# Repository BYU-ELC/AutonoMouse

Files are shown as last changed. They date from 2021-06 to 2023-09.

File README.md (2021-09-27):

# AutonoMouse

## Introduction
Lightweight and low cost autonomous robotics platform for students to gain skills and have fun!

There are two version to this project. 

V1's objective is to build a small autonomous car using Arduino Nano as a controller. The car drives forward until sensing an object. When it senses an object it pivots to both sides to find both distances to the nearest object. It then chooses to travel the distance that is greater. 

V2's objective is to build a similiar autonomous car using ESP32 as a controller. However, this version
allow's the user to put the car into remote control mode where the user can control the car via bluetooth
using an Android smartphone. This doesn't work with an IPhone because there are no opensource bluetooth apps 
that in the App Store. 

## V1 Things to Change
More accessibility Linux and Apple users. Document how to download Arduino IDE and how to interfaces with Arduino devices.

## V2 Things to Change
Finish development for V2. Mostly needs work with the servos.

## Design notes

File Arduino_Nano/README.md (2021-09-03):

# Arduino Nano version of the Autonomouse

## PCB
Recommended: Use gerber files in Build_Files->Chassis1.1->Chasiss1.1_2021-09-01.zip. 

## Acrylic Base
Laser cut the acrylic base using Arduino_Nano_chassis.svg in Build_Files folder. 

## Labs
Follow the labs sequentially in Labs folder.

## Code
Code is provided along with most labs. Upload the code to Arduino Nano using a USB A-Mini and the Arduino IDE.

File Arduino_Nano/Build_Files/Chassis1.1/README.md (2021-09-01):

Chassis1.1 is a revision of the previous Chassis1.0.

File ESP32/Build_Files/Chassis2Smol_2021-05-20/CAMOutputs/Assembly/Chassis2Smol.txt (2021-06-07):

Partlist exported from E:/BYU/ECEN_191_Proj/Chassis2Smol.sch at 5/20/2021 1:57 PM

Qty Value             Device               Package             Parts       Description                                                                                                     POPULARITY PROD_ID    VALUE
1                     CONN_02              1X02                9V_BATT     Multi connection point. Often used as Generic Header-pin footprint for 0.1 inch spaced/style header connections                            
1                     CONN_04PTH           1X04                HC-SR04     Multi connection point. Often used as Generic Header-pin footprint for 0.1 inch spaced/style header connections            CONN-09696      
2                     PINHD-1X19           1X19                JP1, JP2    PIN HEADER                                                                                                      1                          
1   0.1uF             0.1UF-KIT-EZ-50V-20% CAP-PTH-SMALL-KIT   C2          0.1µF ceramic capacitors                                                                                                   CAP-08370  0.1uF
1   0.33uF            0.1UF-KIT-EZ-50V-20% CAP-PTH-SMALL-KIT   C1          0.1µF ceramic capacitors                                                                                                   CAP-08370  0.1uF
1   FRAME-BADGE       FRAME-BADGE          DUMMY               U$1                                                                                                                                                    
1   LM7805            LM7805               TO220H              U2                                                                                                                                                     
2   SERVO             SERVO                1X03                LEFT, RIGHT Servo Motor                                                                                                                                
1   SHOP_ESP_SMOLSMOL SHOP_ESP_SMOLSMOL    ESP32-WROOM-32_SMOL U$2                                                                                                                                                    
1   TL36PO            TL36PO               TL3XPO              S1          TINY SWITCH ON - ON                                                                                             2

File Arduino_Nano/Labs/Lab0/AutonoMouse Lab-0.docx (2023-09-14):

# Introduction

## Summary:

This course is intended for beginning ECEN students taking ECEN 191 at BYU. We assume that students taking this course have a high school level education and are not required to know anything about electrical engineering or hobby engineering. If you are a beginner this is the course for you!

## Learning Outcomes:

The final product from this course is a simple autonomous car named the AutonoMouse. Students will learn the following skills while developing their car:

- Learn what Arduino is
- Learn how to solder pins onto a PCB
- Learn how to code an Arduino Nano
- Learn how to prototype with breadboards
- Learn how LEDs work
- Learn about servos and pulse width modulation signals
- Learn about voltage regulators
- Learn how to spin a servo
- Learn how to use a sensor
- Learn about the HC-SR04
- Learn about PCBs
- System integration
- Troubleshooting

## Materials You Need to Buy:

The following materials you will need to buy yourself:

Arduino Nano
Part | Quantity | Unit Price | Subtotal | Notes
1 inch diameter bottle cap | 2 | | $0.00 | Buy your own, Gatorade bottles work best
Zip ties | 3 | $0.03 | $0.09
Arduino Nano | 1 | $4.00 | $4.00
Switch-SPDT-BB | 1 | $0.06 | $0.06
Voltage Regulator (Q-7805c) | 1 | $1.65 | $1.65
0.1 μF Ceramic Capacitors | 1 | $0.06 | $0.06
0.33 μF Ceramic Capacitor | 1 | $0.06 | $0.06
330 Ohm Resistor | 1 | $0.04 | $0.04
9V Battery | 1 | $1.25 | $1.25
Battery Cap | 1 | $0.44 | $0.44
1x3 Male header | 2 | $0.06 | $0.12
1x4 Female header | 1 | $0.08 | $0.08
2x15 Female header | 2 | $0.30 | $0.60 | You will need to purchase 2 10x1 and 2 5x1 female header pins.
Continuous Servo | 2 | $1.80 | $3.60
PCB | 1 | $1.20 | $1.20 | 3 in^2 @ $0.40 per in^2
Ultra-sonic sensor | 1 | $2.20 | $2.20 | Sensor-Ultrasonic used for angry engineers
LED Colored | 1 | $0.05 | $0.05
CABLE-USB A-Mini | 1 | $0.99 | $0.99
Acrylic | 1 | $1.62 | $1.62 | $0.08 per in^2
Laser Time Acrylic | 2 | $0.06 | $0.12
| | Total | $18.23

Buy these from the ELC (CB 416.) This is a requirement for part of this lab. (This table is just an estimate for these parts, pricing may have changed.) Also, take the time to get acquainted with the ELC. It is a valuable resource on campus.

## Project Requests:

Students can request PCBs, Laser Cuts, and 3D prints from the shop staff. There are two of these for this lab: the PCB and acrylic base. The PCB will be milled and acrylic base laser cut by the shop.

### PCB:

We have a number of these PCB’s already fabricated and should be picked up and paid for with the rest of the autonomouse kit.

First, search the GitHub repository in your web browser (https://github.com/BYU-ELC/AutonoMouse). Then navigate to Arduino_Nano->Build_Files->Chassis1.1 and download the zip file, Chasiss1.1_2021-09-27.zip.

Next, search the ELC project request application (https://byu-elc.mendixcloud.com/p/home) and click the button “PCB Mill Request”. Follow the instructions to fill out the form with your information. You will upload the zip file you just downloaded. The area of the PCB is 3in sq. Things to watch out for: select PCB prototyping for “Requested Service”; single-sided for “Single or Double Sided”; BYU ID # (not netID) for Student ID; and Class for “Purpose”. Click submit.

Once PCB is finished the ELC will let you know when to pick it up.

### Acrylic Base:

We have a number of these Acrylic base’s already fabricated and should be picked up and paid for with the rest of the autonomouse kit.

The acrylic base project request process is similar to the PCB.

First, search the GitHub repository in your web browser (https://github.com/BYU-ELC/AutonoMouse). Then navigate to Arduino_Nano->Build_Files and download Arduino_Nano_chassis.svg. This file will allow the shop to laser cut your car’s base.

Next, search the ELC project request application (https://byu-elc.mendixcloud.com/p/home) and click the button “Laser Cut Request”. Follow the instructions to fill out the form with your information. I would like to use acrylic supplied by the shop. Use any available acrylic on hand (unless you would like to provide or choose your own) for “Material”; 1/8th inch for “Thickness”; BYU ID #, (not netID), for Student ID; Class for “Purpose”; and 4.5-inch x 4.5 inch for “Major Dimension for scaling”. Do not forget to upload the .svg you previously downloaded. Click submit.

After your base is finished the ELC will let you know to pick it up.

## Other:

- 2 x 1-inch diameter bottle caps for wheels (Gatorade or milk bottle caps work nicely for this)
- Computer (this is for programing; a laptop works best because you can bring it into the lab, but a desktop at home would also work)

## Tools Required:

You will need access to the following tools. These can be found in student workshops in the ELC CB41, or you may buy your own as part of your personal electronic kit.

- Breadboard
- Jumper Wires
- Hot glue gun + hot glue
- Soldering station

## How to Access Code for the Labs:

In this course you are not required to know how to code; however, you will still need to know how to download and use Arduino IDE to upload code to your Arduino Nano. Each time the labs ask you to download and upload code go to https://github.com/BYU-ELC/AutonoMouse. This is a GitHub repository that stores all the files for this course. If you’re familiar with GitHub you can git clone the repository. If you’re not familiar then navigate to Arduino_Nano/Labs/(lab# that you’re on). The code file is a .ino file. Copy and paste the code into Arduino IDE and you’ll be good.

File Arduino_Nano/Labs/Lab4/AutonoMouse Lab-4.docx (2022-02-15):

# Lab 4-Sensors

## Learning Outcomes:

- Learn how to work a sensor
- Learn about the ultrasonic sensor

## Background:

Electrical engineers use all kinds of sensors for a variety of applications. It could be a LIDAR module on a self-driving car or a thermocouple in an indoor air conditioning system. Regardless, the purpose of sensors are to record some measurement from the outside world, and turn it into an electrical signal which is then analyzed by a device. Different Types of Sensors and their Uses (i.e. Electrical Sensors) (https://www.thomasnet.com/articles/instruments-controls/sensors/)

Sensors first use an electro-mechanical device to measure something in the real world. The sensor then converts the real-world measurement into a digital or analog signal. A digital signal is composed of bits. Each bit is either a low voltage (0) or high voltage (1). This is what computational devices like your computer use. In contrast, an analog signal can exist within a range of voltages, not just high or low. Regardless of the output type, the sensor communicates the data to a controller from processing. After processing, the controller can then act on the world.

With the advent of the internet of things (Internet of things (https://en.wikipedia.org/wiki/Internet_of_things)), sensors are more important than ever. It’s crucial to understand how they work, and how to use them effectively. When using a sensor that you’re unfamiliar with, it is useful to refer to its datasheet—you can find all sorts of useful information there. For our AutonoMouse we will be using HC-SR04 which is an ultrasonic sensor. Read more about it here: How HC-SR04 Ultrasonic Sensor Works & How to Interface It With Arduino (https://lastminuteengineers.com/arduino-sr04-ultrasonic-sensor-tutorial/)

The project objectives for today’s lab are to:

1) Correctly set up the HC-SR04 ultrasonic sensor

2) Read the data using Arduino’s serial monitor.

### Part 1 Ultrasonic Sensor Circuit:

Build the following circuit.

1. Put Arduino Nano into the center of the breadboard
2. Put wires connect the following pins (Arduino Nano on left, HC-SR04 on right)
  a. 5-volt pin (5V) and VCC
  b. Pin 6 (D6) and TRIG
  c. Pin 7 (D7) and ECHO
  d. Ground pin (GND) and GND

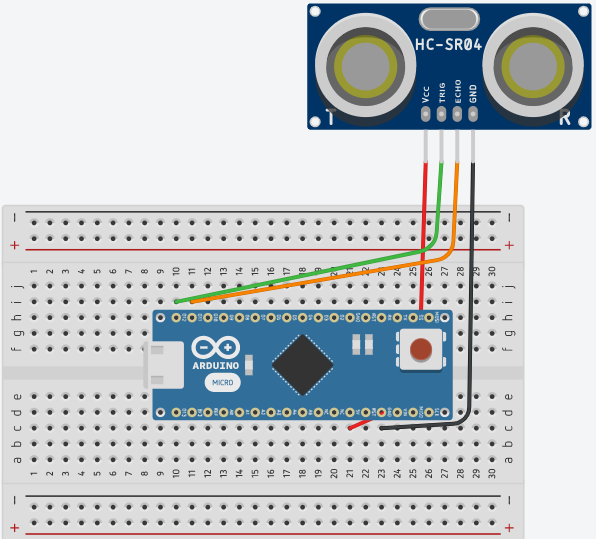
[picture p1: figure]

Ultrasonic Sensor Circuit from Tinkercad

### Part 2 Reading via Serial Monitor:

Copy and upload the code provided with this lab on GitHub to the Arduino. Once the code is successfully uploaded, open a serial monitor through Arduino IDE by clicking the serial monitor button in the top right corner. You should see another window open that provides data from the ultrasonic sensor. Make sure that the baud rate is set to 9600 or else you will see nothing in the serial monitor. The baud rate is the rate information is based through. Try moving the sensor around and get a feel for its range and accuracy. Make sure it works correctly or else your car will not be able to stop in the next lab.

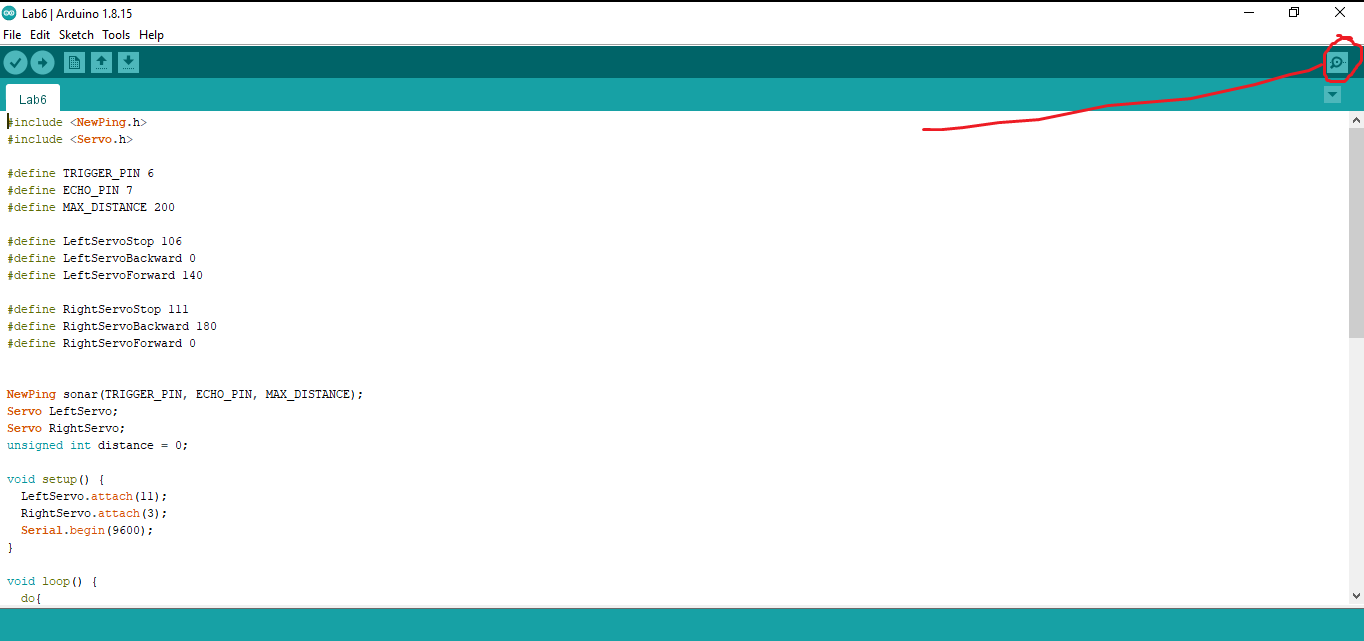
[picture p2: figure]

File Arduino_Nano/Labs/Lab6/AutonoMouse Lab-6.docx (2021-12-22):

# Lab 6-Integration

## Learning Outcomes:

- System integration
- Troubleshooting

## Background:

Up to this point we’ve only tested individual systems of the AutonoMouse (i.e. servos, ultrasonic range finder, PCB). Today we’ll be integrating these subsystems into a whole. This process is called system integration. Integration can sometimes be frustrating because you might not know what system or component is not working. The best thing to do is be patient and logically troubleshoot one thing at a time until you can determine the thing that is not working.

### Part 1 Build:

The first thing we’ll do is attach all our components to our acrylic base mechanically. Then we’ll start connecting the electronics.

1. Use a Phillips screwdriver to poke a hole through the center of your wheels
2. Use hot glue to glue your wheels to your servo mounts
3. Add the screw provided with your servos for extra support
4. Put a dot of hot glue around the circumference of your wheels about every 1cm (this helps the wheel maintain traction
5. Hot glue and zip tie your servos to the two wings of your board
6. Zip tie your battery to the end of the board. Make sure that you insert the zip in the correct manner to create a caster. (From the bottom, insert it through the hole closest to the edge) Check that it’s inserted correctly before tying it

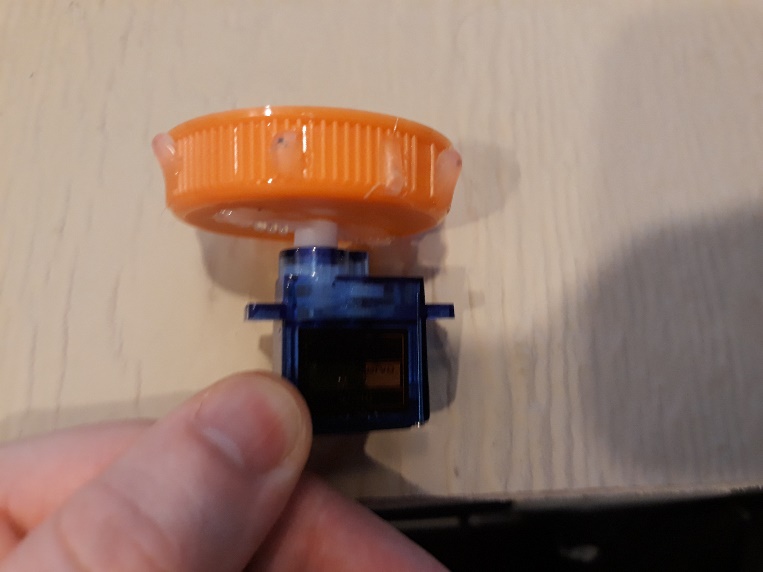
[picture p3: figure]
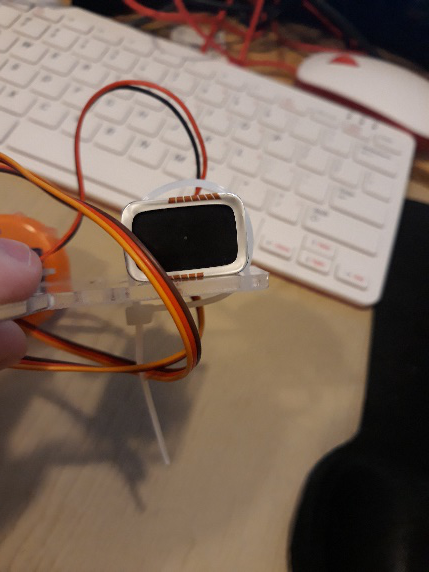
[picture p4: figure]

You may have noticed we haven’t attached the PCB yet. This is because we might need access to the bottom of the PCB to test the electronics next.

### Part 2 Electronics:

1. Run the servo wires through the hole next to the servo, diagonally across the bottom of the board, then back over to the 3 header male pins. Make sure to attach the left servo to the left servo pins and vice versa
2. Upload the code provided for this lab on GitHub
3. Unplug the Arduino from your device, flip the switch, and see if your car is operating correctly.
4. If everything is working correctly (check that it is), it will be hard to remove your PCB. Add some double-sided foam tape to your PCB and attach it to the base.

That's it, you've finished this course. Congratulations!

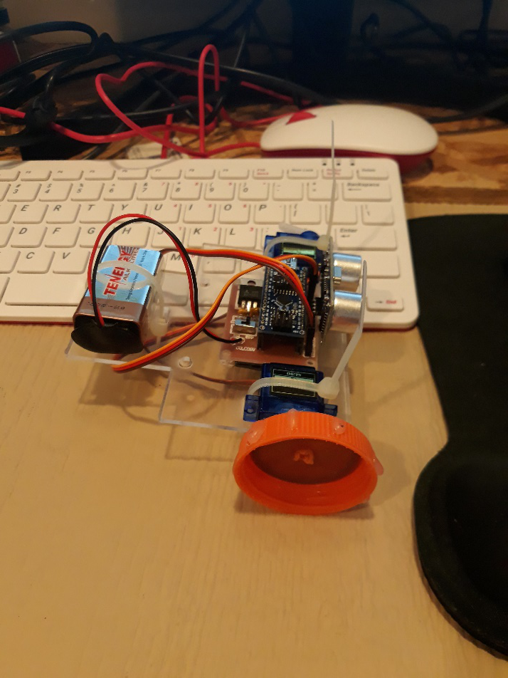
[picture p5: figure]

## Extra Credit:

Try changing the code to make the car do different things.

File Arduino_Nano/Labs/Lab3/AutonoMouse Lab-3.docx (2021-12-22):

# Lab 3-Run a Servo

## Learning Outcomes:

- Learn about servos and pulse width modulation (PWM) signals
- Learn about voltage regulators
- Learn how to spin a servo

## Background:

A servo is a low speed, high torque motor. They are fairly simple to use. Most of these servos are useful because they can determine their angular position using a potentiometer (link (https://en.wikipedia.org/wiki/Potentiometer)). These cheap lightweight control options are used in robotic and hobby aircraft applications where position is a concern. For example, to control aircraft control surfaces. The downside to a potentiometer servo is that it can’t spin more than a certain angle (usually 180deg). The servos that we’ll use are called continuous rotation servos. They remove the potentiometer and essentially operate the same as a motor. However, that comes at the cost of not being able to determine angular position.

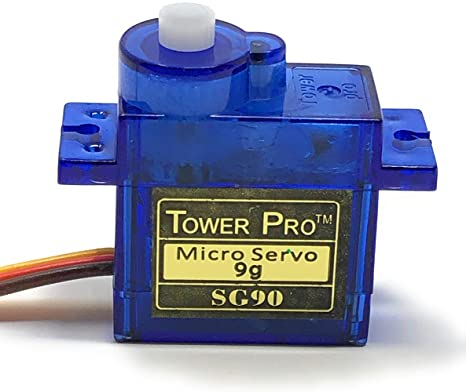
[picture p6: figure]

9g servo. Image courtesy of Amazon (https://www.amazon.com/Tower-Pro-SG90-Analog-Servo/dp/B07B8SJQJD?hvadid=278525945678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).

These servos are simple to use which is why they are used in many applications including hobby aircraft, robotics, drones, etc. We will be using these as the motors for our AutonoMouse. To operate the servos, we only need 3 wires per servo. 1) black for ground, 2) red for 5V power, and 3) orange for a signal (this signal is called pulse-width modulation Pulse-width modulation (https://en.wikipedia.org/wiki/Pulse-width_modulation), Servo control (https://en.wikipedia.org/wiki/Servo_control)).

The objectives for today’s lab are to:

1) Provide the servo with power and a signal from the Arduino Nano

2) Provide the servo with a signal from the Arduino Nano but power from an external source

## Part 1 Power Servo from Arduino Nano:

We will first test out our servo using the 5V pin from our Arduino Nano. This is not good for high current applications because running too much current through the Arduino Nano can break it…so don’t put too much torque on the servo or run it for too long. For a simple test to make it move clockwise or counter-clockwise it’ll be fine.

1. Create the circuit shown below
  a. Connect 5-volt pin (5V) to red
  b. Connect ground pin (GND) to brown
  c. Connect Pin 9 (D9) to orange
2. Copy/paste the code into Arduino IDE from GitHub, and upload it to your Arduino Nano
3. Watch the servo spin clockwise
4. Comment out the first void loop() in the code and uncomment the second (you comment things by adding ‘//’ in front the line of code)
5. Upload your code again and watch your servo spin the other direction.
6. BONUS QUESTION: Continuous servos are controlled in Arduino using the Servo.h library. 0 makes the servo spin fastest in the clockwise direction and 180 makes the servo spin fastest in the counterclockwise direction. 90 makes the servo not spin. (These values might change slightly depending on your servo). Play around with these values to make them spin slower or faster.

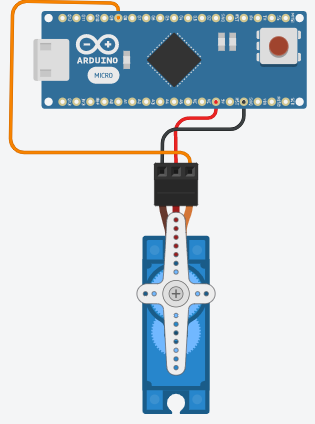
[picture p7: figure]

Circuit created in Tinkercad

## Part 2 Power a Servo using a Voltage Regulator:

Our 9V battery could provide power directly to the servo but the 9V current wouldn’t be good for our 5V rated servo. To limit the voltage, we are going to use a voltage regulator. Like its name suggests, a voltage regulator restricts the voltage to ensure it doesn’t pass a certain threshold. Different regulators are made for different voltage levels. You might have a 3.3, 5V, etc. We will pass the 9V current from the battery through a 5V voltage regulator which will output 5V current to spin the servos.

The voltage regulator we’re using has 3 pins. 1 for output, 2 for ground, and 3 for input voltage. When working with voltage regulators, make sure to consult their datasheets to ensure you use them properly. If you pass too high a current through a voltage regulator you can ruin it. Another thing to remember with voltage regulators is that they can’t increase voltage. The input voltage must be the same or higher than the desired output voltage. They also will get hot after being used for some time.

1. Create the circuit shown below
2. Use the same code as before (the control signal—orange wire—from the Arduino Nano is the same we’re just powering it with something else now)
3. Do the same thing as before (spin the servo clockwise, spin the servo counterclockwise)
4. BONUS QUESTION: how much current is the AN7805 voltage regulator designed to withstand? (Lookup its datasheet online)

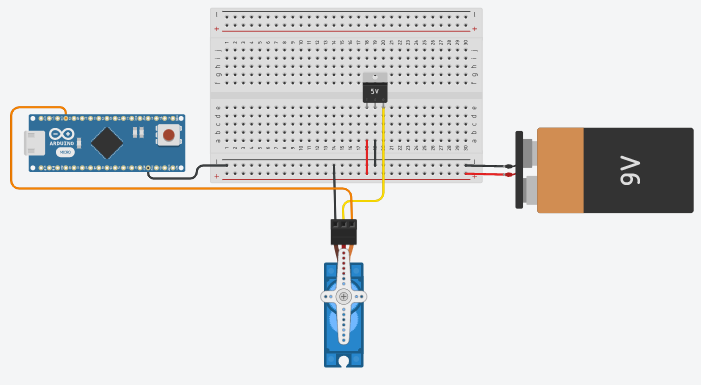
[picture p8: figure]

Circuit created in Tinkercad

### Extra Credit:

Put a wire between power and VIN pin on the Arduino while the battery is plugged in. Your Arduino will then be powered by the battery and can run the code while it’s not plugged into the computer.

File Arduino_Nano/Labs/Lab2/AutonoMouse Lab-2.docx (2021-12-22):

# Lab 2-Blink an LED

## Learning Outcomes:

- Learn how to code Arduino Nano
- Learn prototyping with breadboards
- Learn how LED’s work

## Background:

When working with electronics we usually use a breadboard to prototype our circuit before permanently creating it on a printed circuit board. To finish this lab, you need to show that you can blink an LED with your Arduino Nano.

Before we start creating our circuit please pay attention to a few things:

First, notice how the breadboard is organized: the (-) and (+) rails are connected horizontally, but all other rails are connected vertically in groups of five. This is important to remember and take advantage of when prototyping.

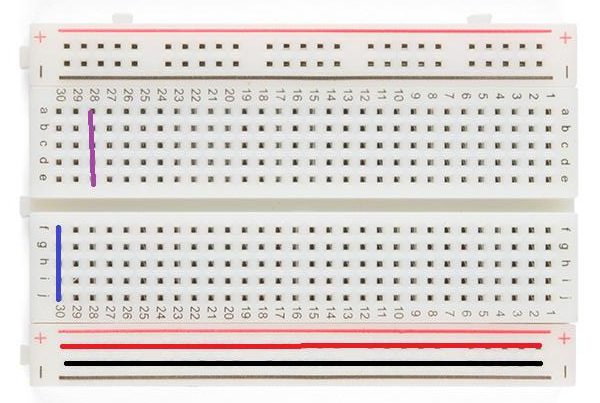
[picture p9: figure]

Breadboard. Image courtesy of Newark.

Second, notice that in the Tinkercad diagram below one side of the LED is bent and the other is straight. This is because an LED is a polarized component (meaning that current only flows one way; if you put it in backwards, the LED won’t turn on). The positive side (bent side) is called the anode, and the negative side (straight side) is called the cathode. Make sure the anode is connected to power, and the cathode is connected to ground.

Third, notice that the LED is in series with the 330-ohm resistor. The LED has almost no resistance, so if we put it directly between power and ground too much current would flow and the LED would burn out. The resistor constricts the current to a much smaller value that the LED can handle.

Fourth, notice that there is a connection between ground on the breadboard and the ground (gnd) pin on the Arduino Nano. Without this connection there would not be a common ground between the board and the Arduino, and the circuit would not work.

The objectives for today’s lab are to:

1) build a circuit on a breadboard to blink an LED

2) install Arduino IDE

3) code our Arduino Nano to blink our LED.

## Step 1 Blink LED Circuit Diagram:

Create the circuit shown in the picture below. (Make sure to push your Arduino Nano far enough into the board to make a connection, but be careful not to break any pins).

1. Place the Arduino in the middle of the breadboard bridging both sides
2. Place a wire from the ground pin (GND) on the Arduino Nano to the (-) rail on the breadboard
3. Place the LED somewhere to the side of the Arduino (don’t place it on any of the same rails that Arduino Nano is on)
4. Place a wire from Pin13 (D13, look for the small white print by the pin) on the Arduino to the anode of the LED
5. Place a 330-ohm resistor (look up resistor band chart) between the - rail and the cathode of the LED

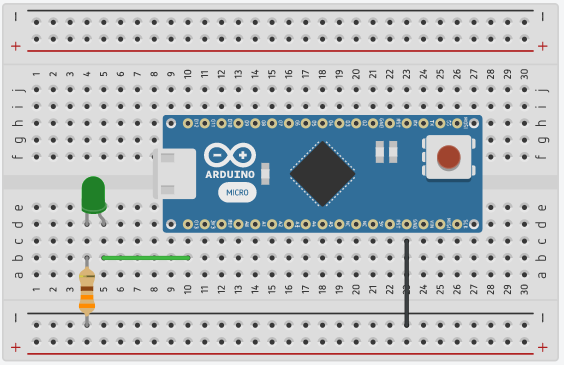
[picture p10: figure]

Circuit diagram from Tinkercad

## Step 2 Downloading Arduino Software:

How to Install Arduino Software (IDE) on Windows 10 (https://www.youtube.com/watch?v=TbHsOgtCMDc)

You are not required to learn much about coding in this course, however, you will still need to learn to download and use the Arduino integrated development environment (Arduino IDE). An IDE is software that helps you program the specific microcontroller/microprocessor you’re using. The Arduino IDE is small and simple to use. Choose your operating system and follow the instructions to download Arduino IDE at Getting Started with Arduino products (https://www.arduino.cc/en/Guide). Scroll down and follow the instructions under Install the Arduino Desktop IDE header.

Once you’ve installed the Arduino IDE, copy and paste the code provided from GitHub into the IDE. Code for blinking light. (https://github.com/BYU-ELC/AutonoMouse/blob/master/Arduino_Nano/Labs/Lab2/lab2/lab2.ino)

Once you're done copying the code we will now try to get it to interface with your Arduino Nano.

1. Open the IDE
2. Plug in your Arduino Nano via USB
3. In Tools/Board: select “Arduino Nano” (this tells the IDE what controller to expect)

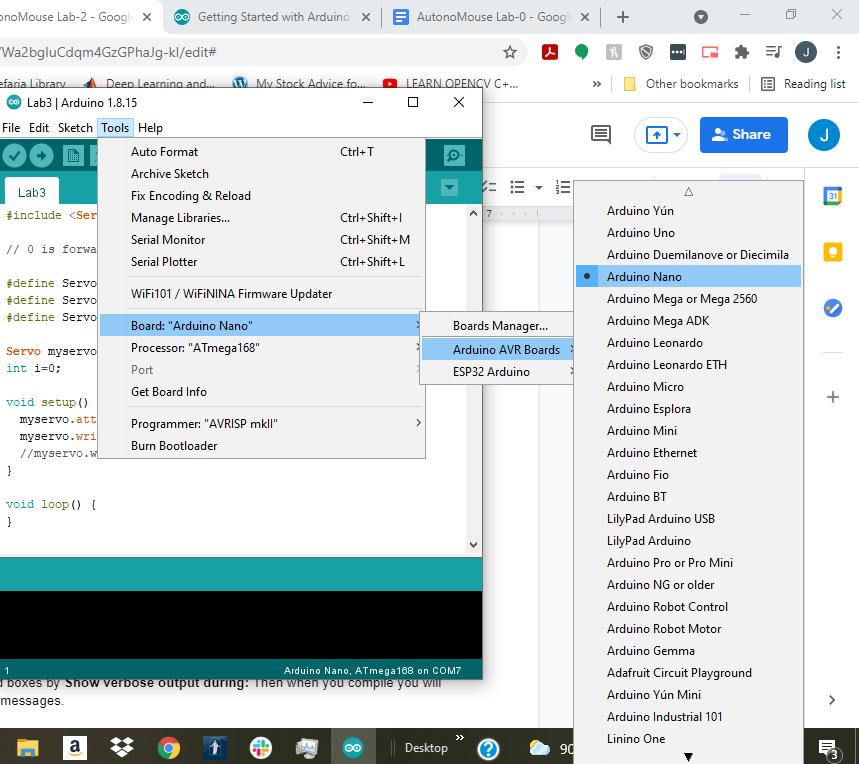
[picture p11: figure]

4. In Tools/Processor: select the processor that your Arduino Nano uses. I’m using a board with ATmega168. (if you get an error “avrdude: stk500_recv(): programmer is not responding” then change which processor you’re using)

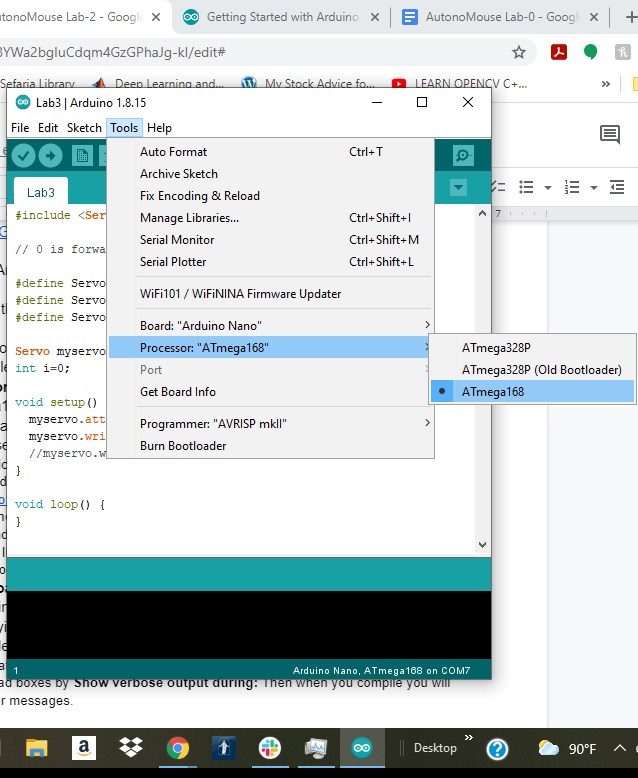
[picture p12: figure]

5. Under Tools/Port select which port on your computer the Arduino Nano is plugged into. Note: this might be tricky. My computer’s USB driver wasn’t compatible with Arduino and it wouldn’t install the Arduino drivers which came with Arduino IDE so I found a CH340 Driver at https://sparks.gogo.co.nz/ch340.html that worked. First go to device manager (on windows) and look under ports for the port your Arduino is connected to. (An easy way to do this is to plug in your Arduino nano and see if a new port will pop up) If it does then you should be able to select which port in Arduino IDE. If not, check if an unidentified USB device came up instead. If that’s the case then you need to install a compatible driver.

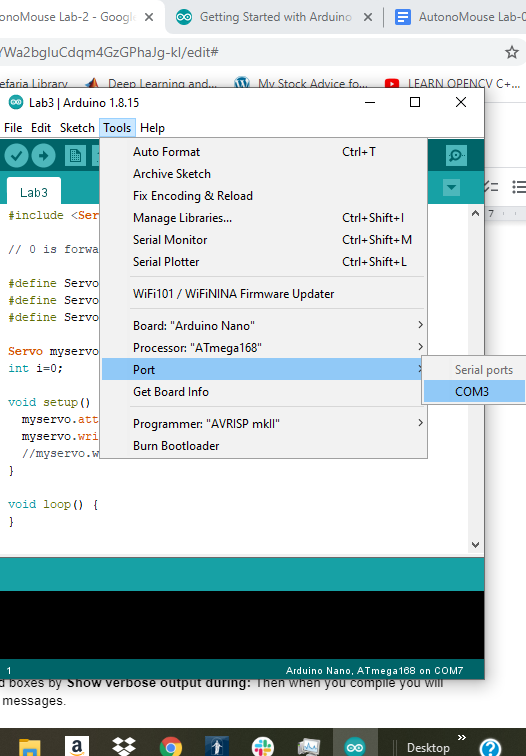
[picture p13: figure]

6. Select Sketch/Upload to upload the software onto the Arduino Nano. If it worked, your Arduino Nano should start doing what you told it to do. If not, you will see error messages saying that your code compiled incorrectly. You will need to fix whatever is causing the problem. Note: it’s helpful sometimes to get the whole error message when you’re debugging what went wrong. To change these settings, go to File/Preferences and select compilation and upload boxes by Show verbose output during: Then when you compile you will get the complete error messages.

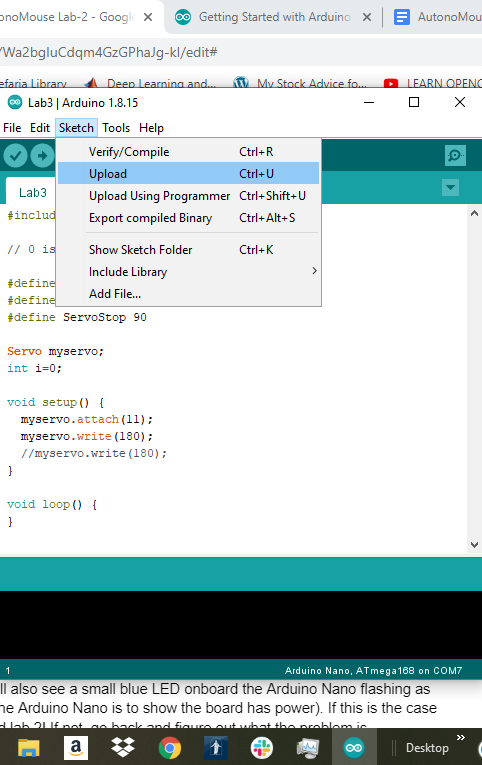
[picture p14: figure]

## Step 3 Blinking the LED:

If you did steps 1 and 2 correctly then you should see the LED turn on for a second and then turn off for a second. You will also see a small blue LED onboard the Arduino Nano flashing as well (the red LED onboard the Arduino Nano is to show the board has power). If this is the case congratulations! You finished lab 2! If not, go back and figure out what the problem is.

### Bonus Questions:

How could you get the LED to go on for 2 seconds followed by 1 second off?

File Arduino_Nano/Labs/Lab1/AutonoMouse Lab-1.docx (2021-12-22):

# Lab 1-Soldering Arduino

## Learning Outcomes:

- I know what Arduino is
- I can solder pins onto an Arduino Nano

## Background:

Arduino is a simple and easy to use hardware and software platform. They are reasonably inexpensive, open source, and easy-to-use. Arduino sells different types of boards which are better for different kinds of projects. Arduino Uno is probably the most popular board.

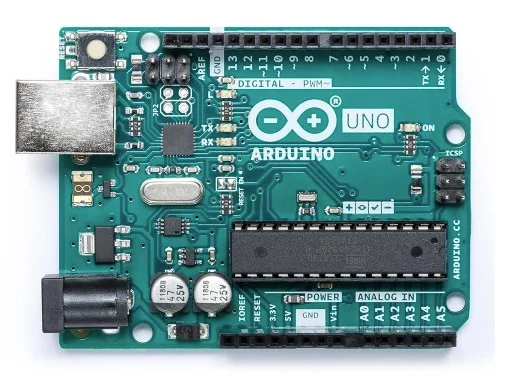
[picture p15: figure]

Arduino Uno. Image courtesy of Arduino (https://store.arduino.cc/usa/arduino-uno-rev3)

The board that we’ll be using is a shrunken version of Arduino Uno called Arduino Nano.

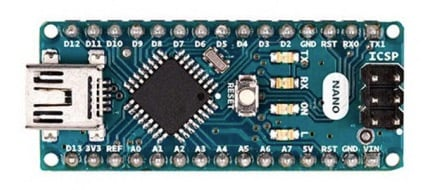
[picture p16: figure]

Arduino Nano. Image courtesy of Arduino (https://store.arduino.cc/usa/arduino-nano)

Because of its smaller size the Arduino Nano is better fit for some projects where space is a concern.

Arduino boards utilize a component called a microcontroller. The microcontroller is the little black square on the nano and the black rectangle on the uno. The specific microcontroller for the Arduino Nano is typically an ATmega168 or ATmega 328. Microcontrollers are different from microprocessors. A microcontroller is optimized to perform a specific task repeatedly; however, it is not like a computer which uses microprocessors and can perform a variety of tasks. (More on the difference between microcontrollers and microprocessors here (https://www.guru99.com/difference-between-microprocessor-and-microcontroller.html)) This means when we upload code to our Arduino it will run that code forever until it dies or we cut the power.

The objective for today’s lab is to:

1) solder pins onto our Arduino Nano.

### Step 1 Soldering Arduino Nano:

The Arduino you received probably doesn’t have pins attached quite yet. The method we use to attach them is called soldering.

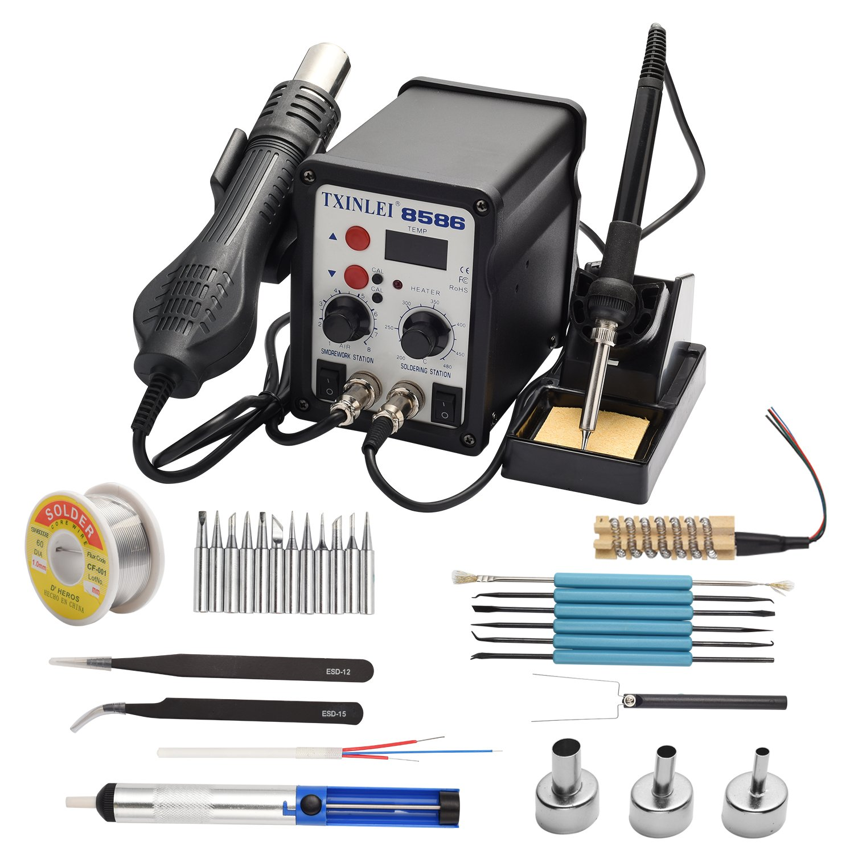
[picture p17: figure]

Soldering Station. Image courtesy of Amazon (https://www.amazon.com/TXINLEI-8586-Soldering-Different-Desoldering/dp/B07FJ6PNHF).

Soldering is the process of joining two metal parts together using a metal filler. Solder is what we call the metal filler we melt and flow to join the parts together. It might help you to think of the solder as the glue that holds the two parts together and the soldering iron as a hot glue gun.

#### Tools and Materials:

To solder our Arduino Nano, we will need:

1. the components we want to solder (i.e. Arduino Nano and pins)
2. soldering wire
3. a soldering iron
4. a fan or well-ventilated area

#### Safety:

CAUTION: It is important that you follow the proper safety procedures to not harm yourself or others!

- Don’t touch the tip of the soldering iron while it is hot. Return it to the stand when you are finished soldering a component to avoid accidentally touching it.
- Work in a well-ventilated area and use a fan to avoid ingesting smoke from the solder. Lead solder fumes are hazardous. Solder containing a rosin-based flux produces fumes that can result in occupational asthma, worsen existing asthmatic conditions, and can cause eye and upper respiratory tract irritation.
- Solder usually contains lead, which is poisonous. Do not eat or drink while soldering. Wash your hands after using solder.

#### Soldering:

Start soldering by first making a mechanical connection between the two components you want to solder. This means to hold them in place before trying to apply the solder. You can use the helping hands to assist with this, but for the Arduino Nano use your breadboard. Place your header pins into the breadboard and put the Arduino PCB onto the pins. Using the breadboard this way makes sure the pins are perpendicular with the board.

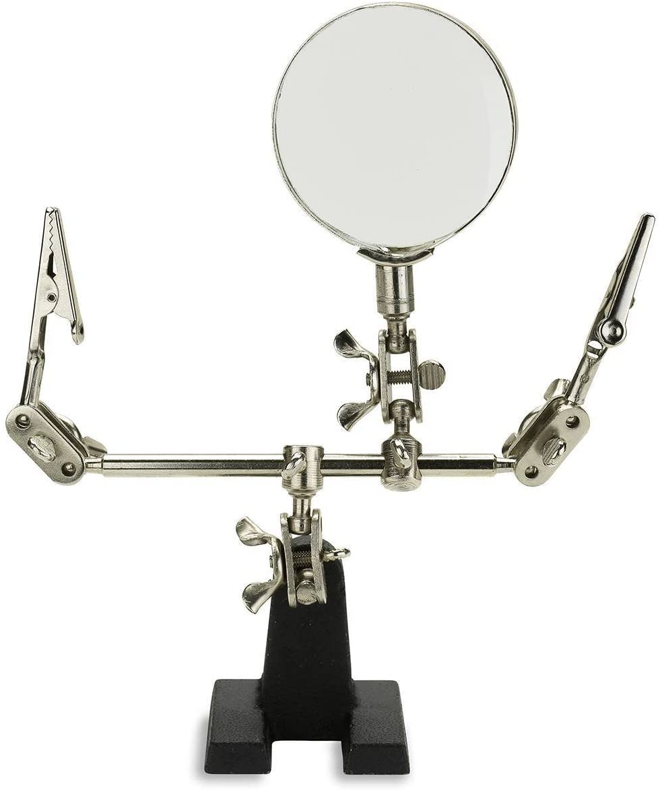
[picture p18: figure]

Helping hands. Image courtesy of Amazon.

Next, heat the components with the tip of your soldering iron before trying to apply the solder. When the connection is hot, push the soldering wire into the joint. The solder should melt and bind to the parts. Don’t melt the solder and then try to apply it to the joint—it will not work. You want the solder to bind to the Arduino Nano and the pins. If done improperly you will have a poor joint which will not allow electricity to flow.

#### Tips:

- You can apply a small amount of solder to the tip of your iron before heating the joint. This is called tinning and will help the solder iron conduct heat better.
- Use a small amount of solder each time. It’s easier to add solder than to take it away. If you do end up using too much you can remove solder using a desoldering gun.
- Use a multimeter to check continuity as you go along. There is nothing more frustrating than soldering a bunch of components, and then finding out there’s a short somewhere but you don’t know which component it might be. (Watch the continuity videos below for more information)

#### Extra Materials:

Please read/watch these extra materials before soldering. It will really help you to do a better job and avoid having to desolder a shorted Arduino Nano.

BEST RESOURCE: How-To-Videos (https://ece.byu.edu/how-to-videos)

How to Solder an Arduino Nano (https://www.youtube.com/watch?v=wDbUChzxIrE)

Electronics Primer: How to Solder Electronic Components (https://www.sciencebuddies.org/science-fair-projects/references/how-to-solder)

Soldering Tutorial for Beginners: Five Easy Steps (https://www.youtube.com/watch?v=Qps9woUGkvI)

Multimeters - Resistance and Continuity (https://www.youtube.com/watch?v=ckWVNQ4Ci4A)

Ohms vs. Continuity for HVAC techs (https://www.youtube.com/watch?v=KbTcO1vWDnc)

Once you’re done soldering the pins the finished Arduino Nano should look something like this:

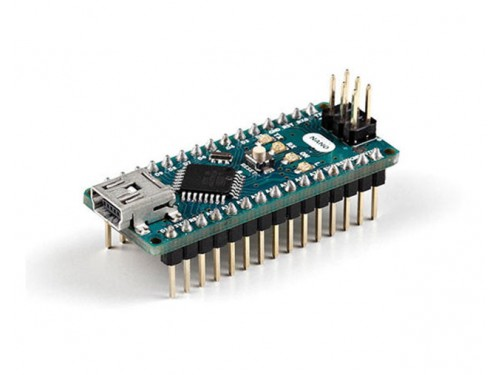
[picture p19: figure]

Finished Arduino Nano. Image courtesy of Arduino (https://store.arduino.cc/usa/arduino-nano)

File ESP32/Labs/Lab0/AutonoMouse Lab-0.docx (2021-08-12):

# Introduction

## Summary:

This course is intended for beginning ECEN students taking ECEN 191 at BYU. We assume that students taking this course have a high school level education and are not required to know anything about electrical engineering or hobby engineering. If you are a beginner this is the course for you.

## Learning Outcomes:

The final product from this course is a simple autonomous car named the AutonoMouse. Students will learn the following skills while developing their car:

- Learn what Arduino is
- Learn how to solder pins onto a PCB
- Learn how to code Arduino Nano
- Learn prototyping with breadboards
- Learn how LED’s work
- Learn about servos/pwms
- Learn about voltage regulators
- Learn how how to spin a servo
- Learn how to work a sensor
- Learn about HC-SR04
- Learn about PCBs
- Learn to solder a PCB
- System integration
- Troubleshooting

## Materials You Need To Buy:

The following materials you will need to buy yourself:

- 2 Bottle Caps for wheels (Gatorade caps work nicely for this)
- Computer (this is for programing, a laptop works best because you can bring it into the lab but a desktop at home would also work)

## Tools Required:

You will need the following tools. These can be found in CB413.

- Breadboard??
- Jumper Wires??
- Hot glue gun+hot glue
- Soldering station
- USB-A or USB-C (depending on the computer) to USB Mini-B
- Double sided foam tape

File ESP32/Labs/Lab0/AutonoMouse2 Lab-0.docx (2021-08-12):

# Lab 0 – Collect Materials

## Learning Outcomes:

- Learn about the AutonoMouse Project
- Collect Materials for the project

## Background:

The AutonoMouse project was made for BYU’s ECEN 191 New Student Seminar. Students taking the course will choose between a variety of projects the AutonoMouse being one of them.

## Getting Credit

You will learn many things during this course. Including: breadboards, LEDs, pulse width modulation, circuit boards, microcontrollers, servos, etc. There are a total of 7 labs, this being the first one. For each lab you will generally follow an outline how to build a certain part of the AutonoMouse and then submit a Learning Suite quiz for credit. Make sure to submit the Learning Suite quiz or you will not receive credit for completing a lab.

## Getting Help

If you are stuck at any point along this course, and you probably will be, make sure to take advantage of the resources available to you. A frustrating bug in a computer program or a flaw in your design can be solved in a few minutes by getting help than by trying to do it alone.

One place is the student workstations next to the Experiential Learning Center (ELC) room 413 in the Clyde building. The shop assistants are occasionally available to answer questions and the other students there can be a valuable resource. \

Another place is your student study groups. Ask your friends to help you and make sure to help them.

## Getting Materials

You are required to buy the following materials for this course:

ESP32 w/RC
Part | Quantity | Unit Price | Subtotal
Zip ties | 3 | $0.03 | $0.09
ESP32 | 1 | $4.50 | $4.50
Switch-SPDT-BB | 1 | $0.06 | $0.06
Voltage Regulator (Q-7805c) | 1 | $1.65 | $1.65
0.1 uF Ceramic Capacitors | 1 | $0.06 | $0.06
0.33 uF Ceramic Capacitor | 1 | $0.06 | $0.06
9V Battery | 1 | $1.25 | $1.25
Battery Cap | 1 | $0.44 | $0.44
Male header Pins | 6 | $0.02 | $0.12
Female Header Pins | 42 | $0.02 | $0.84
servos | 0 | $1.80 | $0.00
PCB | 4 | $0.40 | $1.60
Double Sided Foam Tape | 1 | | $0.00
Sonar Sensor | 1 | $2.20 | $2.20
Laser Time | 2 | $0.06 | $0.12
Servos | 2 | $1.80 | $3.60
Micro usb to usb-A cord
Acrylic? | 1 | | $0.00
| | Total | $16.59

Buy them from the electrical engineering shop. It will be much cheaper than any place you can find online and they know exactly which parts you need. While you’re there take your time to get acquainted with what services the shop offers.

## Learning Suite Quiz

Make sure to go online and submit the Learning Suite quiz associated with this lab.

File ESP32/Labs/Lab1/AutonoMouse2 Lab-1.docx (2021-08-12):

# Lab 1 - Blink an LED

Adapted tutorial from randomnerdtutorials.com https://randomnerdtutorials.com/getting-started-with-esp32/

## Learning Outcomes:

- Learn about esp2
- Blink an LED

## Background:

ESP32:

ESP32 is a series of low-cost microcontrollers with a built-in wifi and bluetooth module. A microcontroller is an integrated circuit with a small amount of memory and other resources that executes a program over and over again. It is different from your computer in that your computer runs an operating system that can change which task it’s working on. A microcontroller doesn’t run an operating system so it will execute the task you gave it until it's powered off or it’s memory is changed.

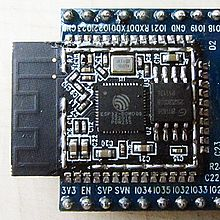
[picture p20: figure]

Inside an ESP-WROOM-32 Module. Image Courtesy of Wikipedia.

We will be using the DOIT DEVIT V1 ESP32-WROOM-32 Development Board to run our RC/AutonoMouse car. Before we build our car we will learn how each subsystem works and test each to ensure that they work.

Video about ESP32: Introduction to ESP32 - Getting Started (https://www.youtube.com/watch?v=xPlN_Tk3VLQ) (0:00-10:25)

Video about microcontrollers: What is a Microcontroller? (https://www.youtube.com/watch?v=jKT4H0bstH8)

Breadboards:

When working with electronics we usually use a breadboard to prototype our circuit before permanently creating it on a printed circuit board. To finish this lab you need to show that you can blink an LED with your esp32.

Before we start creating our circuit please pay attention to a few things:

First, notice that the breadboard is organized a certain way. The (-) and (+) rails are connected horizontally, but all other rails are connected vertically. This is important to remember and take advantage of while prototyping.

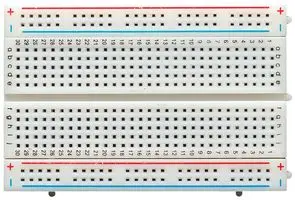
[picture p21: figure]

Breadboard. Image courtesy of Newark.

Second, notice that in the diagram below one side of the LED is bent and the other is straight. This is because an LED is a polarized component (meaning that current only flows one way, if you put it in backwards the LED won’t turn on). The positive side (bent side) is called the anode and the negative side (straight side) is called the cathode. Make sure the anode is connected to power and the cathode is connected to ground.

Third, notice that the LED is in series with the 330 ohm resistor. The LED has almost no resistance and if we put it directly between power and ground too much current would flow and break the LED. The resistor constricts the current to a much smaller value that the LED can handle.

Fourth, notice that there is a connection between ground on the breadboard and the ground (gnd) pin on the esp32. Without this connection there would not be a common ground between the board and the arduino, and the circuit would not work.

The objectives for today’s lab are to:

1) build a circuit on a breadboard to blink an LED

2) install Arduino IDE

3) code our esp32 to blink our LED

## Step 1 Blink LED Circuit Diagram:

Create the circuit shown in the picture below. (the board used in the picture here is an Arduino Nano, use your esp32 instead and make sure to use the correct pins) Push the esp32 far enough into the board to make a connection but be careful not to break any pins).

1. Place the esp32 in the middle of the breadboard bridging both sides
2. Place a wire from the ground pin (gnd) on the esp32 to the (-) rail on the breadboard
3. Place the LED somewhere to the side of the esp32 (don’t place it on any of the same rails that esp32 is on)
4. Place a wire from D25 on the esp32 to the anode of the LED
5. Place a 330 ohm resistor (look up resistor band chart) between the (-) rail and the cathode of the LED

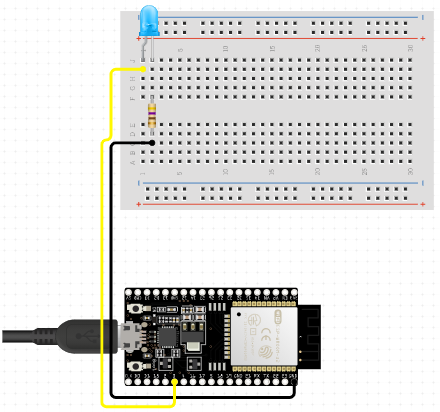
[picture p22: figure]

Circuit diagram from circuito.io

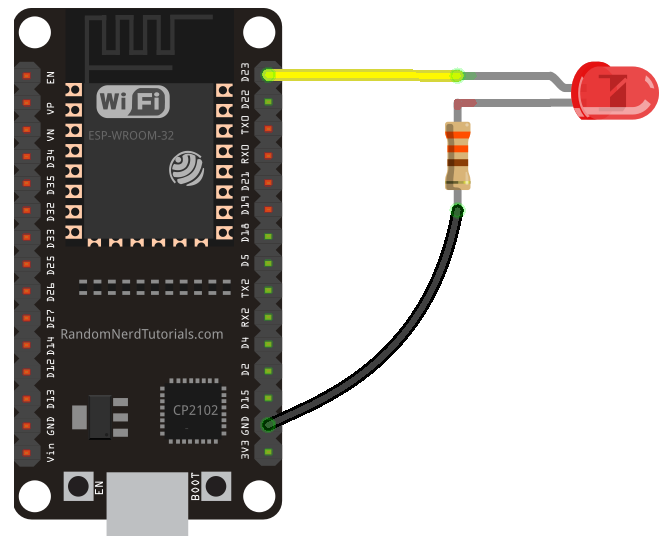
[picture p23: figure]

Image courtesy of randomnerdtutorials.com

59 thoughts on “Getting Started with the ESP32 Development Board” (https://randomnerdtutorials.com/getting-started-with-esp32/)

## Step 2 Downloading Arduino Software:

How to Install Arduino Software (IDE) on Windows 10 (https://www.youtube.com/watch?v=TbHsOgtCMDc)

You are not required to learn much about coding in this course, however, you will still need to learn to download and use the Arduino integrated development environment (Arduino IDE). The esp32 is coded the same way you would code an Arduino. An IDE is software that helps you as the programmer program the specific microcontroller/microprocessor you’re using. The Arduino IDE is small and simple to use. Choose your operating system and follow the instructions to download Arduino IDE at Getting Started with Arduino products (https://www.arduino.cc/en/Guide).

Once you’ve installed the Arduino IDE we need to download one last package to allow it to work with esp32. Follow the download instructions in this video: Introduction to ESP32 - Getting Started (https://www.youtube.com/watch?v=xPlN_Tk3VLQ) (10:25-12:30)

Once you're done we will now try to get it to interface with your esp32.

1. Open the IDE
2. Plug in your esp32 via usb (you will need a usb-A to micro-usb)
3. In Tools/Board: select “DOIT ESP32 DEVKIT V1” (if you don’t see this option then go back and make sure you followed the steps correctly to download the esp32 library in Introduction to ESP32 - Getting Started (https://www.youtube.com/watch?v=xPlN_Tk3VLQ) (10:25-12:30))

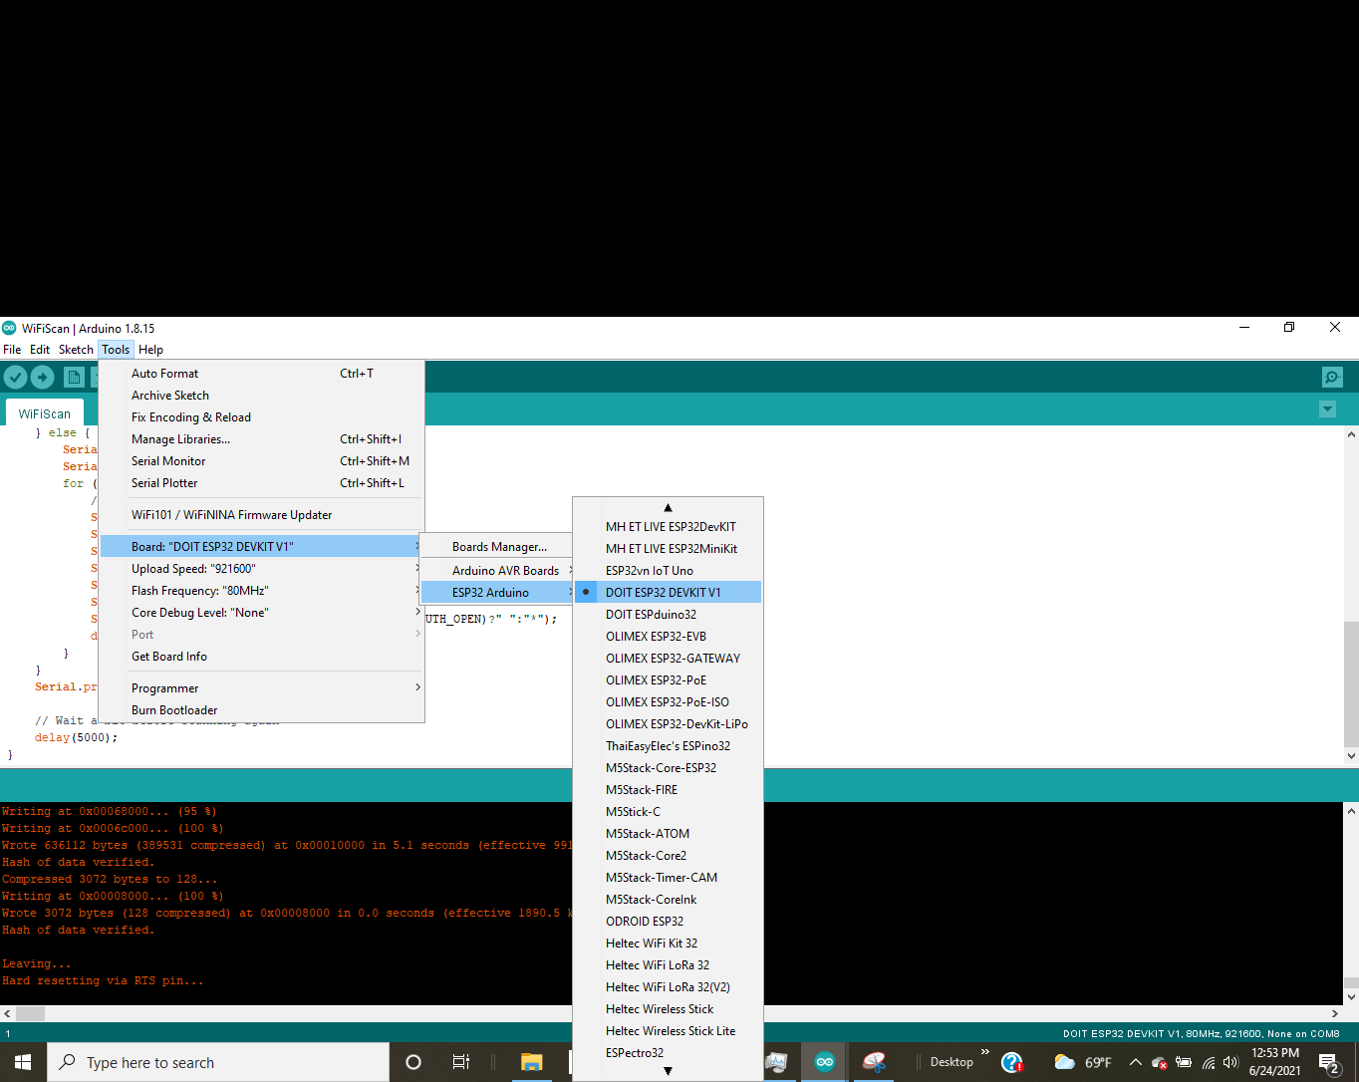
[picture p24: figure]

4. Make sure Tools/Upload Speed is 921600, Tools/Flash Frequency is 80MHz, and Tools/Core Debug Level is set to “None”.
5. Under Tools/Port select which port on your computer the esp32 is plugged into. Note: this might be tricky. My computer’s usb driver wasn’t compatible with arduino and it wouldn’t install the arduino drivers which came with arduino IDE so I found a CH340 Driver at CH340 Drivers for Windows, Mac and Linux (https://sparks.gogo.co.nz/ch340.html) that worked. First go to device manager (on windows) and look under ports for the port your arduino is connected to. (an easy way to do this is to plug in your arduino nano and see if a new port will pop up) If it does then you should be able to select which port in arduino IDE. If not, check if an unidentified usb device came up instead. If that’s the case then you need to install a compatible driver. Need to figure out how it works with MAC and Linux


6. Select Sketch/Upload to upload the software onto the device. If it worked correctly your esp32 should start doing what you told it to do. If not, you will see error messages saying that your code compiled incorrectly. You will need to fix whatever is causing the problem. Note: it’s helpful sometimes to get the whole error message when you’re debugging what went wrong. To change these settings go to File/Preferences and select compilation and upload boxes by Show verbose output during:. Then when you compile you will get the complete error messages.


## Step 3 Blinking the LED:

If you did steps 1 and 2 correctly then you should see the LED turn on for a second and then turn off for a second. If this is the case congratulations!

Troubleshooting Resources:

Try pushing the onboard enable button if the code doesn’t immediately run.

Look at the troubleshooting section of Installing ESP32 in Arduino IDE (Windows, Mac OS X, Linux) (https://randomnerdtutorials.com/installing-the-esp32-board-in-arduino-ide-windows-instructions/) if the code doesn’t upload correctly.

### Bonus Question:

Change the time the LED is on by adjusting the values passed to the delay function in the code. The delay function takes a number as an argument and waits for that amount of time in milliseconds (eg 1000 milliseconds = 1 second)

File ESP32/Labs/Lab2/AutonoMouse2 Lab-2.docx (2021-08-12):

# Lab 2 - ESP32 Bluetooth

Adapted tutorial from randomnerdtutorials.com https://randomnerdtutorials.com/esp32-bluetooth-classic-arduino-ide/

## Learning Outcomes:

- Connect to esp32 bluetooth module
- Blink led with commands via bluetooth

## Background:

The esp32 comes with an onboard bluetooth module. This allows us to connect directly to it without any other hardware. We could do this lab with an Arduino board but it requires us to attach a bluetooth module.

## Step 1 Download Serial Bluetooth Terminal:

For this lab you will need an Android phone. Go to the Play Store and download the Serial Bluetooth Terminal app. It looks like this:


## Step 2 Download and Upload Code:

Copy paste the code provided with this lab into the Arduino IDE. Then flash the code to your board. After the code uploads, open the Serial Monitor at a baud rate of 115200. Press the ESP32 Enable Button. It’s the one that has RST by it, not BOOT.

After a few seconds, you should get a message saying: “The device started now you can pair it with bluetooth!”.

## Step 3 Connect:

Enable Bluetooth on your phone. Open the Serial Bluetooth App, To connect with a new device click the Devices tab. Select Pair new device. You’ll then see a list of available devices. Select the ESP32test device. Go back to the terminal and you should see output like this:


Try typing something in the terminal on your phone. You should also see the message on the serial monitor. And vice versa.

## Step 4 Turn on Led via BT:

Next we will be lighting an LED via BT. First create the circuit in the picture below, minus the thermometer connected to GPIO 32.


Copy and paste the code provided into the IDE. Upload it to the ESP32. After the code flashes you should be able to turn the LED on by typing “led_on” and “led_off” in the terminal.


We can also assign a button to each message. Go to the menu and select Edit Macros. Create a name for each and assign “led_on”, and “led_off” for the values. Make it text edit mode. You now can control the led by pressing your button.

You can also edit the button’s by long pressing them.

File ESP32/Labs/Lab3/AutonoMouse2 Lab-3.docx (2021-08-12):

# Lab 3 - Drive a Servo

Adapted tutorial from randomnerdtutorials.com https://randomnerdtutorials.com/getting-started-with-esp32/

## Learning Outcomes:

- Learn about servos/pwms
- Learn about voltage regulators
- Learn how to spin a servo
- Spin a servo using bluetooth

## Background:

A servo is a low speed high torque motor. They are fairly simple to use. Most of these servos are useful because they can determine their angular position using a potentiometer (link (https://en.wikipedia.org/wiki/Potentiometer)). These cheap lightweight control options are used in robotic and hobby aircraft applications where position is a concern. For example, to control aircraft control surfaces. The downside to a potentiometer servo is that it can’t spin more than a certain angle (usually 180deg). The servos that we’ll use are called continuous rotation servos. They remove the potentiometer and essentially operate the same as a motor. However, that comes at the cost of not being able to determine angular position.


9g servo. Image courtesy of Amazon (https://www.amazon.com/Tower-Pro-SG90-Analog-Servo/dp/B07B8SJQJD?hvadid=278525945678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).

These servos are simple to use which is why they are used in many applications including hobby aircraft, robotics, drones, etc. We will be using these as the motors for our AutonoMouse. To operate the servos we only need 3 wires per servo. 1) black for ground, 2) red for 5V power, and 3) orange for a signal (this signal is called pulse-width modulation Pulse-width modulation (https://en.wikipedia.org/wiki/Pulse-width_modulation), Servo control (https://en.wikipedia.org/wiki/Servo_control)).

The objectives for today’s lab are to:

1) power the servo with power and a signal from the Arduino Nano

2) power the servo via external power source

3) power the servo via external power source and connect via bluetooth.

## Step 1 Power Servo from ESP32:

We will first test our servo using the 5V pin from our esp32. This is not good for high current applications because running too much current through the esp32 can break it, so don’t put too much torque on the servo or run it for too long. For a simple test to make it move clockwise and counter-clockwise it’ll be fine.

1. Create the circuit shown below
  a. Connect 5V to red
  b. Connect ground to brown
  c. Connect Pin0 to orange
2. Copy/paste the Lab3-2.ino into Arduino IDE and upload to your Arduino Nano
3. Watch the servo spin clockwise
4. Comment out the first void loop() in the code and uncomment the second (you comment things by adding ‘//’ in front the line of code)
5. Upload your code again and watch your servo spin the other direction.
6. BONUS QUESTION: Continuous servos are controlled in Arduino using the Servo.h library. 0 makes the servo spin fastest in the clockwise direction and 180 makes the servo spin fastest in the counterclockwise direction. 90 makes the servo not spin. (These values might change slightly depending on your servo). Play around with these values to make them spin slower or faster.


Circuit created in circuito.io

## Part 2 Power Servo using a Voltage Regulator:

We can power our servo using an external power source. For this part we will use a 9V. However, running 9 volts (V) through a 5V rated servo would damage it. To decrease the voltage we are going to use a voltage regulator. A voltage regulator ensures that the voltage doesn’t increase past a certain level. Different regulators are made for different voltage levels. You might have a 3.3, 5V, etc. We will pass the 9V current from the battery through a 5V voltage regulator, which will output 5V, to spin the servos.

The voltage regulator we’re using has 3 pins. 1 for output, 2 for ground, and 3 for input voltage. When working with voltage regulators make sure to consult their datasheets to make sure not to use them improperly. If you pass too high a current through a voltage regulator you can ruin it. Another thing that to remember with voltage regulators is that they can’t increase voltage. The input voltage must be the same or lower than the desired output voltage. They also will get hot after being used for some time.

1. Create the circuit shown below (substitute the esp32 for the Arduino Nano, connect the signal wire to pin0 on the esp32)
2. Use the same code as before (the signal wire, orange colored wire, from the Arduino Nano is the same we’re just powering it with something else now)
3. Do the same thing as before. Spin the servo clockwise, spin the servo counterclockwise)
4. BONUS QUESTION: how much current can the AN7805 voltage regulator withstand. (Lookup its datasheet online)


Circuit created in Tinkercad

## Part 3 Control a Servo via bluetooth:

To finish this lab we will now control our servo circuit from part 2 using our bluetooth serial app from the last lab.

First, make the circuit from part 2.

Next, download, paste, and upload Lab3-1.ino provided in this lab to the esp32 using Arduino IDE.

Next, use your phone serial bluetooth app to connect to the esp32 like the last lab. You should receive a similar message as last time: “The device started now you can pair it with bluetooth!”.

Lastly, create 3 buttons to send a text object. Make them send text variables labeled “servo_clockwise”, “servo_counter-clockwise”, and “servo_off”. Double check that your spelling is correct otherwise it won’t work.


Test your bluetooth connection by turning your servo on and off using your phone. You can also survey what is being outputted by using Arduino IDE’s serial monitor. Make sure that the baud rate is set to 115200.

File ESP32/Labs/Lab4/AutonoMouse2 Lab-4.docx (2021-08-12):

# Lab 4-Sensors

Tutorial adapted from https://www.instructables.com/Pocket-Size-Ultrasonic-Measuring-Tool-With-ESP32/

## Learning Outcomes:

- Learn how to work a sensor
- Learn about the ultrasonic sensor
- Connect with the sensor using bluetooth

## Background:

Electrical engineers use all kinds of sensors for a variety of applications. It could be a LIDAR module on a self-driving car or a thermocouple in an indoor air conditioning system. Regardless, the purpose of sensors is to record some measurement from the outside world, turn it into an electrical signal, which is then analyzed by a device. Different Types of Sensors and their Uses (ie Electrical Sensors) (https://www.thomasnet.com/articles/instruments-controls/sensors/#applications)

Sensors first use an electro-mechanical device to measure something in the real world. The sensor then converts the real-world measurement into a digital or analog signal. A digital signal is composed of bits. Each bit is either a low voltage, 0’s or high voltage, 1’s. This is what computational devices like your computer use. An analog signal can exist within a range of voltages. Regardless, this signal is typically sent to a controller which then processes that signal and will then act on the world.

With the advent of the internet of things (Internet of things (https://en.wikipedia.org/wiki/Internet_of_things)) sensors are more important than ever. It’s important to understand how they work and use them effectively. When using a sensor that you’re unfamiliar with it is useful to refer to its datasheet. You can find all sorts of useful information there. For our AutonoMouse we will be using HC-SR04 which is an ultrasonic sensor. Read more about it here: How HC-SR04 Ultrasonic Sensor Works & How to Interface It With Arduino (https://lastminuteengineers.com/arduino-sr04-ultrasonic-sensor-tutorial/)

The project objectives for today’s lab are to:

1) read data from an ultrasonic sensor (HC-SR04)

2) read the data using arduino’s Serial monitor

### Part 1 Ultrasonic Sensor Circuit:

Build the following circuit.

1. Put Arduino Nano into the center of the breadboard
2. Put wires connect the following pins (esp32 on left, HC-SR04 on right
  a. 5V and VCC
  b. D2 and TRIG
  c. D5 and ECHO
  d. Gnd and Gnd


(The picture shows 3.3V and VCC, use the 5V pin instead)

### Part 2 Reading via Serial Monitor:

Copy and upload the code provided with this lab to the esp32. Once the code is successfully uploaded, open a serial monitor through Arduino IDE by clicking the serial monitor button in the top right corner. You should see another window open that provides data from the ultrasonic sensor. Make sure that the baud rate is set to 115200 or else you will see nothing in the serial monitor. The baud rate is the rate information is based through. Try moving the sensor around and get a feel for the range and how accurate it is. Make sure it works correctly or else your car will not be able to stop in the next lab.


### Part 3 Reading via bluetooth:

Now we will do the same thing as before but connect via bluetooth. Copy the same circuit as in part 2. Copy and upload the other code provided with the lab to the esp32. Connect via bluetooth using the serial app. It should show the same readings as the serial monitor. You can turn the sensor on and off by sending “HC-SR04_on” and “HC-SR04_off” respectively.

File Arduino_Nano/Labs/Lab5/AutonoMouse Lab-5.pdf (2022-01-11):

# Lab 5-Soldering a PCB

## Learning Outcomes:

- Learn about PCBs
- Learn to solder a PCB

## Background:

Printed circuit boards (PCBs) are an important part of most modern electronics. Electronic circuits use many different components, and these components communicate through the PCB. A PCB consists of a flat sheet of insulating material and a layer of copper. The copper layer is then mechanically or chemically etched into separate tracks called traces. These traces are the ‘wires’ of the PCB connecting each individual component in the proper manner.


Arduino Nano. Image courtesy of Arduino

The Arduino Nano above includes a PCB. The Arduino Nano’s components are all mounted onto the PCB (blue wafer), and you can see it’s traces between the components on the front and back.

There are two different types of PCB components. One component is called “through-hole” and the other is called “surface mount”. Each offers its own pros and cons. Through-hole components have leads that are inserted through holes on the board, thus the name, and soldered into copper traces on the copper side. Through-hole manufactured boards are easier for humans to make because they are bigger than surface mounted components; however, they also take up more space.


Through-hole pcb. Image courtesy of wellpcb.com.

Surface mounted PCB technology came about in the 1960s and gained widespread popularity by the mid-1990s. Components were designed to mount directly to the surface of the PCB. This cuts down on their size allowing more compact design. However, it makes manual soldering a pain. Robots are typically used to place and solder these components.


Surface Mounted PCB. Image courtesy of neodenusa

The ELC has a PCB mill. The mill is a mechanical through-hole mill. Because it’s mechanical, the boards are cheap and not as high quality as a chemical commercial PCB manufacturer. The copper PCBs in your kit are from the ELC PCB mill.


ELC Copper PCBs

For the next part of this lab, you will solder on components to your PCB and learn how to test for connectivity between each of them.

### Part 1 Solder a PCB:

1. Gather your components (PCB, voltage regulator, switch, 0.1uF capacitor, 0.33uF capacitor, battery cap, 2 3-pin male headers, 1 4-pin female header, 2 15-pin female headers)
2. Find a solder station
3. Follow the board layout and solder each of your components to the top of the PCB
4. As you’re going along, use a multimeter set to connectivity setting to check each connection on your PCB. For example, each trace should connect each of the pin’s part of its circuit but should not connect other traces. If you by chance have solder connecting two different traces then you have a shorted circuit. That will make your car fail. (Look at lab 1 for extra material on testing connectivity)

Once you’ve finished, your PCB should look something like this:


If you’ve checked to make sure you didn’t short anything,


place your Arduino Nano into the header pins. Make sure to check the orientation.

### Part 2 Test the PCB:

Try inserting and testing a servo using the code provided from lab 3 or inserting and testing the HC-SR04 ultrasonic sensor from lab4. If you soldered your PCB correctly you should get the same results as before. Make sure it works or your car will not work for the final lab.

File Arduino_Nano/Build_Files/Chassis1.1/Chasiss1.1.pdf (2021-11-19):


11/19/2021 3:46 PM f=4.00 C: \

U sers\ShopTechs\D ocum ents\EAG LE\projects\Autonom ouse\C hasiss1.1.brd

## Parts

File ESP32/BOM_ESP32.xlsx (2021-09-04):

ESP32 w/RC
Part | Quantity | Unit Price | Subtotal
1 inch bottle cap | 2 |  | $0.00 | Gatorade bottles work best
Zip ties | 3 | $0.03 | $0.09
ESP32 | 1 | $4.50 | $4.50
Switch-SPDT-BB | 1 | $0.06 | $0.06
Voltage Regulator (Q-7805c) | 1 | $1.65 | $1.65
0.1 uF Ceramic Capacitors | 1 | $0.06 | $0.06
0.33 uF Ceramic Capacitor | 1 | $0.06 | $0.06
9V Battery | 1 | $1.25 | $1.25
Battery Cap | 1 | $0.44 | $0.44 |  | *0.08
Male header Pins |  | $0.02 | $0.00
Female Header Pins |  | $0.02 | $0.00
Continuous Servo | 2 | $1.80 | $3.60
PCB | 4 | $0.40 | $1.60 | $0.40 per in^2
Sonar Sensor | 1 | $2.20 | $2.20
Laser Time | 2 | $0.06 | $0.12
CABLE-USB A-Micro | 1 | $0.60 | $0.60
Laser Time Acrylic | 2 | $0.06 | $0.12
Acrylic? | 1 | $1.62 | $1.62 | $0.08 per in^2
 |  | Total | $17.97

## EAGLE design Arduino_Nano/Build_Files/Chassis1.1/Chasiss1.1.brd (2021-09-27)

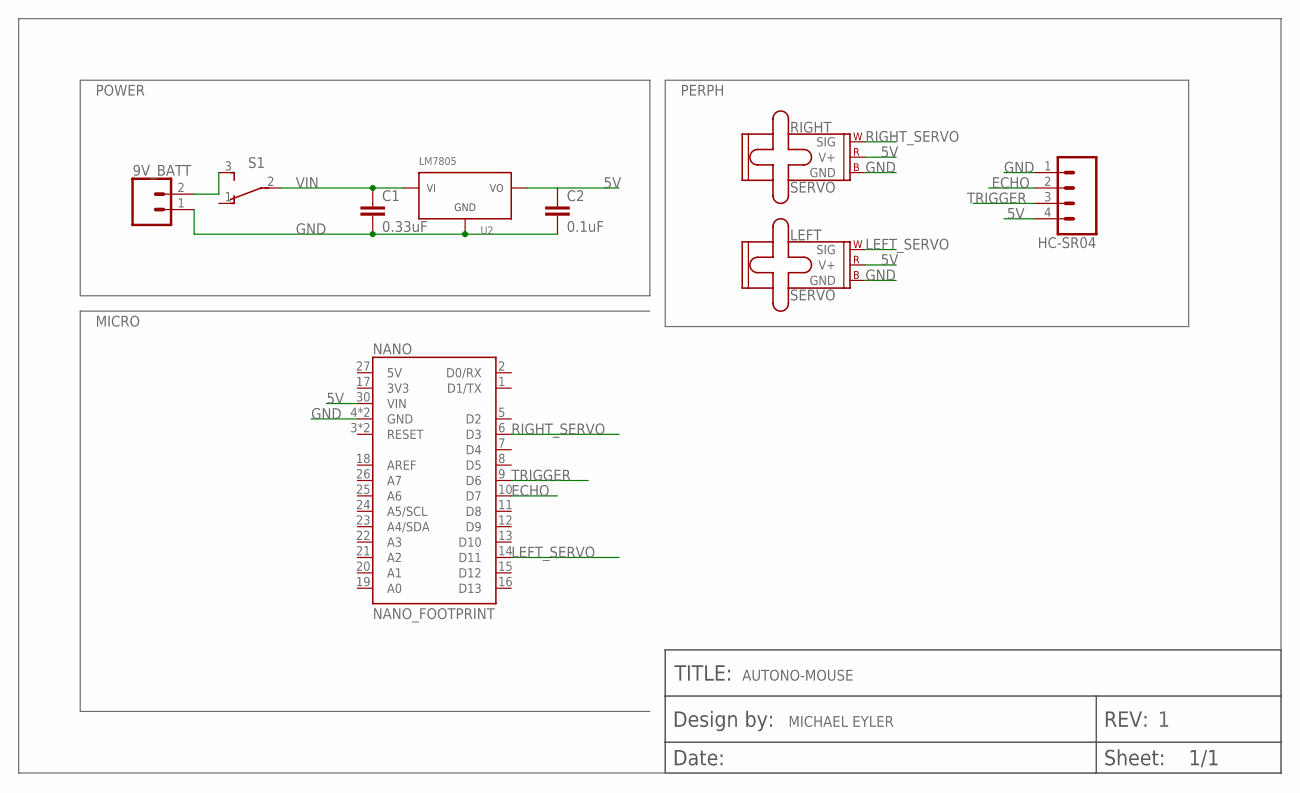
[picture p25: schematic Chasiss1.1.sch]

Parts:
9V_BATT: CONN_02; 1X02
C1: 0.33uF; CAP-PTH-SMALL-KIT
C2: 0.1uF; CAP-PTH-SMALL-KIT
HC-SR04: CONN_04PTH; 1X04
LEFT: SERVO; 1X03
NANO: NANO_FOOTPRINT; NANO
RIGHT: SERVO; 1X03
S1: TL36PO; TL3XPO
U2: LM7805; TO220H
U$1: FRAME-BADGE; DUMMY

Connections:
5V: C2.1, HC-SR04.4, LEFT.2 (V+), NANO.30 (VIN), RIGHT.2 (V+), U2.3 (VOUT)
ECHO: HC-SR04.2, NANO.10 (D7)
GND: 9V_BATT.1, C1.2, C2.2, HC-SR04.1, LEFT.3 (GND), NANO.4 (GND), NANO.29 (GND), RIGHT.3 (GND), U2.2 (GND)
LEFT_SERVO: LEFT.1 (SIG), NANO.14 (D11)
unnamed: 9V_BATT.2, S1.3 (S)
RIGHT_SERVO: NANO.6 (D3), RIGHT.1 (SIG)
TRIGGER: HC-SR04.3, NANO.9 (D6)
VIN: C1.1, S1.2, U2.1 (VIN)

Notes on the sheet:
POWER
PERPH
MICRO
MICHAEL EYLER
AUTONO-MOUSE

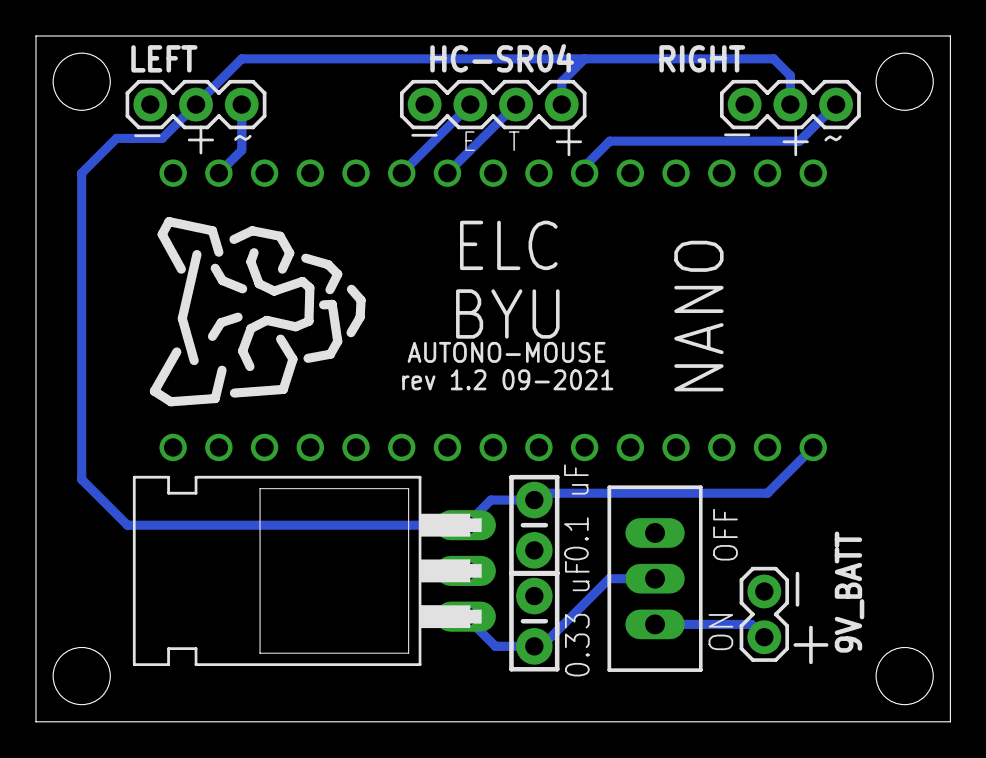
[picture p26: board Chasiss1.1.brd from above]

Board: 2 copper layers, 50.8 x 38.1 mm, 10 parts (0 on the bottom side), 8 nets.

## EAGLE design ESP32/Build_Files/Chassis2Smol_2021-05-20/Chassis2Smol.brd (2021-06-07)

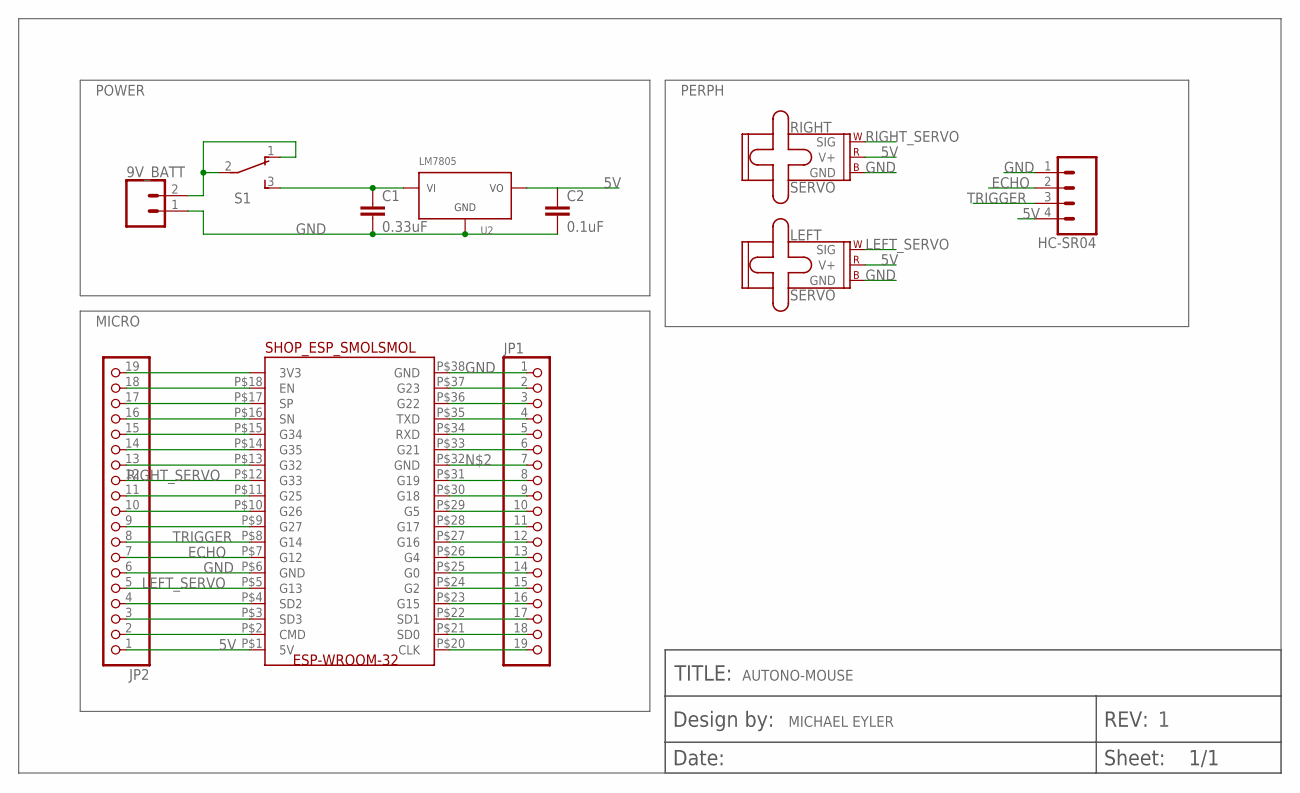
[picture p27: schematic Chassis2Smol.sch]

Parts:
9V_BATT: CONN_02; 1X02
C1: 0.33uF; CAP-PTH-SMALL-KIT
C2: 0.1uF; CAP-PTH-SMALL-KIT
HC-SR04: CONN_04PTH; 1X04
JP1, JP2: PINHD-1X19; 1X19
LEFT: SERVO; 1X03
RIGHT: SERVO; 1X03
S1: TL36PO; TL3XPO
U2: LM7805; TO220H
U$1: FRAME-BADGE; DUMMY
U$2: SHOP_ESP_SMOLSMOL; ESP32-WROOM-32_SMOL

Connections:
5V: C2.1, HC-SR04.4, JP2.1, LEFT.2 (V+), RIGHT.2 (V+), U2.3 (VOUT), U$2.P$1 (5V)
ECHO: HC-SR04.2, JP2.7, U$2.P$7 (G12)
GND: 9V_BATT.1, C1.2, C2.2, HC-SR04.1, JP1.1, JP2.6, LEFT.3 (GND), RIGHT.3 (GND), U2.2 (GND), U$2.P$6 (GND), U$2.P$38 (GND)
LEFT_SERVO: JP2.5, LEFT.1 (SIG), U$2.P$5 (G13)
unnamed: 9V_BATT.2, S1.1 (O), S1.2
unnamed: JP1.7, U$2.P$32 (GND)
unnamed: JP2.19, U$2.P$19 (3V3)
unnamed: JP2.18, U$2.P$18 (EN)
unnamed: JP2.17, U$2.P$17 (SP)
unnamed: JP2.16, U$2.P$16 (SN)
unnamed: JP2.15, U$2.P$15 (G34)
unnamed: JP2.14, U$2.P$14 (G35)
unnamed: JP2.13, U$2.P$13 (G32)
unnamed: JP2.11, U$2.P$11 (G25)
unnamed: JP2.10, U$2.P$10 (G26)
unnamed: JP2.9, U$2.P$9 (G27)
unnamed: JP2.4, U$2.P$4 (SD2)
unnamed: JP2.3, U$2.P$3 (SD3)
unnamed: JP2.2, U$2.P$2 (CMD)
unnamed: JP1.19, U$2.P$20 (CLK)
unnamed: JP1.18, U$2.P$21 (SD0)
unnamed: JP1.17, U$2.P$22 (SD1)
unnamed: JP1.2, U$2.P$37 (G23)
unnamed: JP1.3, U$2.P$36 (G22)
unnamed: JP1.4, U$2.P$35 (TXD)
unnamed: JP1.5, U$2.P$34 (RXD)
unnamed: JP1.6, U$2.P$33 (G21)
unnamed: JP1.8, U$2.P$31 (G19)
unnamed: JP1.9, U$2.P$30 (G18)
unnamed: JP1.10, U$2.P$29 (G5)
unnamed: JP1.11, U$2.P$28 (G17)
unnamed: JP1.12, U$2.P$27 (G16)
unnamed: JP1.13, U$2.P$26 (G4)
unnamed: JP1.14, U$2.P$25 (G0)
unnamed: JP1.15, U$2.P$24 (G2)
unnamed: JP1.16, U$2.P$23 (G15)
RIGHT_SERVO: JP2.12, RIGHT.1 (SIG), U$2.P$12 (G33)
TRIGGER: HC-SR04.3, JP2.8, U$2.P$8 (G14)
VIN: C1.1, S1.3 (S), U2.1 (VIN)

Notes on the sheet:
POWER
PERPH
MICRO
MICHAEL EYLER
AUTONO-MOUSE

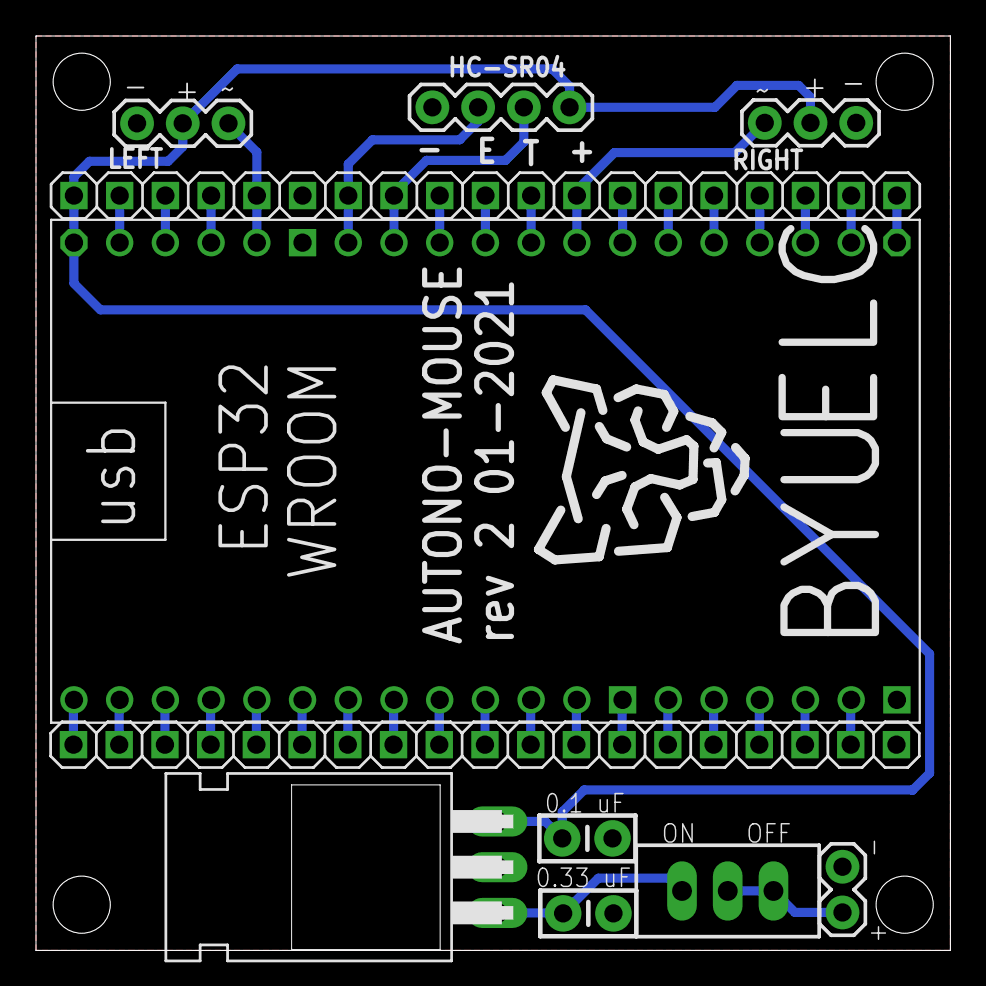
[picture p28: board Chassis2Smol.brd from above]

Board: 2 copper layers, 50.8 x 50.8 mm, 12 parts (0 on the bottom side), 39 nets.

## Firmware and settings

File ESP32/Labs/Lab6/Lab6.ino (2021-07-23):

/*
 * Code created by Joshua Miller
 * 23 July 2021 for BYU's ECEN 191 course
 * 
 * modified code from John Bennett 
 * https://dronebotworkshop.com/esp32-servo/
 * 
 * modified code from Rui Santos
 * Complete project detials at https://randomnerdtutorials.com
 * 
 */

// Load libraries
#include <ESP32Servo.h>
#include "BluetoothSerial.h"
#include <NewPing.h>

// Check if Bluetooth configs are enabled
#if !defined(CONFIG_BT_ENABLED) || !defined(CONFIG_BLUEDROID_ENABLED)
#error Bluetooth is not enabled! Please run `make menuconfig` to and enable it
#endif

// Ultrasonic Parmeters
#define TRIGGER_PIN 6
#define ECHO_PIN 7
#define MAX_DISTANCE 200

// Servo objects
Servo myRservo; // create servo object to control the right servo
Servo myLservo; // create servo object to control the left servo
// 16 servo objects can be created on the ESP32

//Ultrasonic Object
NewPing sonar(TRIGGER_PIN, ECHO_PIN, MAX_DISTANCE);
unsigned int distance = 0;

// Bluetooth Serial object
BluetoothSerial SerialBT;

// Handle received and sent messages
String message = "";
char incomingChar;

// State control variable. 0 is autonomous control, 1 is RC
int state = 0;

// Recommended PWM GPIO pins on the ESP32 include 2,7,12-19,21-23,25-27,32-33
// motor pins 13, 12
int rServoPin = 13;
int lServoPin = 12;

// Speed variable for the servos. 0<=speed<=90, 90 fastest
int speed = 10;

void setup() {
  // Allow allocation of all timers
  ESP32PWM::allocateTimer(0);
  ESP32PWM::allocateTimer(1);
  ESP32PWM::allocateTimer(2);
  ESP32PWM::allocateTimer(3);
  myRservo.setPeriodHertz(50);
  myLservo.setPeriodHertz(50);
  myRservo.attach(rServoPin, 500, 2400); // attaches the right servo on pin 13
  myLservo.attach(lServoPin, 500, 2400); // attaches the left servo on pin 12
  // using default min/max of 1000us and 2000us
  // different servos may require different min/max settings

  Serial.begin(115200);
  // Bluetooth device name
  SerialBT.begin("ESP32");
  Serial.println("The device started, now you can pair it with bluetooth!");
}

void loop() {
  while (SerialBT.available()){
    char incomingChar = SerialBT.read();
    Serial.println(incomingChar);

    if (incomingChar == 'x') {
      ChangeState();
    }
    // Check recieved message and control output accordingly
    if (state == 1) {
        // RC control
      switch(incomingChar){
        // G F I
        // L S R
        // H B J
        case 'S':
          // Do nothing
          RightServoStop();
          LeftServoStop();
          break;
        case 'F':
          // Forwards
          RightServoForward(speed);
          LeftServoForward(speed);
          break;
        case 'B':
          // Backwards
          RightServoBackward(speed);
          LeftServoBackward(speed);
          break;
        case 'L':
          // Turn left
          RightServoForward(speed);
          LeftServoBackward(speed);
          break;
        case 'R':
          // turn right
          RightServoBackward(speed);
          LeftServoForward(speed);
          break;
        case 'G':
          // slight forward left
          RightServoForward(speed);
          LeftServoForward(speed/2);
          break;
        case 'I':
          // slight forward right
          RightServoForward(speed/2);
          LeftServoForward(speed);
          break;
        case 'H':
          // slight backward left
          RightServoBackward(speed);
          LeftServoBackward(speed/2);
          break;
        case 'J':
          // slight backward right
          RightServoBackward(speed/2);
          LeftServoBackward(speed);
          break;
        case '1':
          speed = 10;
          break;
        case '2':
          speed = 20;
          break;
        case '3':
          speed = 30;
          break;
        case '4':
          speed = 40;
          break;
        case '5':
          speed = 50;
          break;
        case '6':
          speed = 60;
          break;
        case '7':
          speed = 70;
          break;
        case '8':
          speed = 80;
          break;
        case '9':
          speed = 90;
          break;
      }
    }
    else if (state == 0){
      // Autonomous control
      delay(250);
      distance = sonar.ping_cm();
      Serial.print(distance);
      Serial.println("cm");
      if (distance < 10 && distance != 0){ // sensor registers 0 if longer than 200cm
        Serial.print("Obstacle");
        delay(500);
        RightServoBackward(speed);
        LeftServoBackward(speed);
        delay(500);
        // pivot left
        RightServoForward(speed);
        LeftServoBackward(speed);
        delay(500);
        // check distance
        distance = sonar.ping_cm();
        Serial.print(distance);
        Serial.println("cm");
        int leftDist = distance;
        // pivot right
        RightServoBackward(speed);
        LeftServoForward(speed);
        delay(1000);
        int rightDist = distance;
        // check distance
        if (leftDist > rightDist){
          RightServoForward(speed);
          LeftServoBackward(speed);
          delay(1000);
        }
        // drive the longer of the two
      }      
      RightServoForward(speed);
      LeftServoForward(speed);
    }
    else{
      Serial.println("ERROR!!!");
    }
  }
}

void ChangeState(){
  // This only works if there are 2 states
  if (state == 0){
    state = 1;
  }
  else{
    state = 0;
  }
}

void LeftServoStop(){
  myLservo.write(90);
}

void RightServoStop(){
  myRservo.write(90);
}

void LeftServoForward(int speed){
  myLservo.write(90+speed);
}

void RightServoForward(int speed){
  myRservo.write(90-speed);
}

void LeftServoBackward(int speed){
  myLservo.write(90-speed);
}

void RightServoBackward(int speed){
  myRservo.write(90+speed);
}

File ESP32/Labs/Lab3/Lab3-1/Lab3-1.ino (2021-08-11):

/* Sweep
 by BARRAGAN <http://barraganstudio.com>
 This example code is in the public domain.

 modified 22 July 2021
 by Josh Miller

 * Modifications were made to this code for BYU's ECEN 191 class. This code is being used to 
 * Drive a continuous servo not a normal servo. 

 modified 8 Nov 2013
 by Scott Fitzgerald
 
 modified for the ESP32 on March 2017
 by John Bennett
 
 see http://www.arduino.cc/en/Tutorial/Sweep for a description of the original code
 
 * Different servos require different pulse widths to vary servo angle, but the range is 
 * an approximately 500-2500 microsecond pulse every 20ms (50Hz). In general, hobbyist servos
 * sweep 180 degrees, so the lowest number in the published range for a particular servo
 * represents an angle of 0 degrees, the middle of the range represents 90 degrees, and the top
 * of the range represents 180 degrees. So for example, if the range is 1000us to 2000us,
 * 1000us would equal an angle of 0, 1500us would equal 90 degrees, and 2000us would equal 1800
 * degrees.
 * 
 * Circuit: (using an ESP32 Thing from Sparkfun)
 * Servo motors have three wires: power, ground, and signal. The power wire is typically red,
 * the ground wire is typically black or brown, and the signal wire is typically yellow,
 * orange or white. Since the ESP32 can supply limited current at only 3.3V, and servos draw
 * considerable power, we will connect servo power to the VBat pin of the ESP32 (located
 * near the USB connector). THIS IS ONLY APPROPRIATE FOR SMALL SERVOS. 
 * 
 * We could also connect servo power to a separate external
 * power source (as long as we connect all of the grounds (ESP32, servo, and external power).
 * In this example, we just connect ESP32 ground to servo ground. The servo signal pins
 * connect to any available GPIO pins on the ESP32 (in this example, we use pin 18.
 * 
 * In this example, we assume a Tower Pro MG995 large servo connected to an external power source.
 * The published min and max for this servo is 1000 and 2000, respectively, so the defaults are fine.
 * These values actually drive the servos a little past 0 and 180, so
 * if you are particular, adjust the min and max values to match your needs.
 */
 
#include <ESP32Servo.h>
 
Servo myservo;  // create servo object to control a servo
// 16 servo objects can be created on the ESP32
 
int pos = 0;    // variable to store the servo position
// Recommended PWM GPIO pins on the ESP32 include 2,4,12-19,21-23,25-27,32-33 
int servoPin = 13;
 
void setup() {
  // Allow allocation of all timers
  ESP32PWM::allocateTimer(0);
  ESP32PWM::allocateTimer(1);
  ESP32PWM::allocateTimer(2);
  ESP32PWM::allocateTimer(3);
  myservo.setPeriodHertz(50);    // standard 50 hz servo
  myservo.attach(servoPin, 500, 2400); // attaches the servo on pin 18 to the servo object
  // using default min/max of 1000us and 2000us
  // different servos may require different min/max settings
  // for an accurate 0 to 180 sweep
}
 
void loop() {
  myservo.write(180); // drive motor counter-clockwise for 5 seconds // COMMENT OUT THESE TWO LINES
  delay(5000);
//  myservo.write(0); // drive motor counter-clockwise for 5 seconds // UNCOMMENT OUT THESE TWO LINES
//  delay(5000);

//  myservo.write(90); // stop motor for 1 second
//  delay(1000);
//  myservo.write(0); // try to drive motor clockwise for 5 seconds
//  delay(5000);
//  myservo.write(90); // stop motor for 1 second
//  delay(1000);
}

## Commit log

2021-06-26 Uploaded Arduino labs and code
    [Chassis1.brd, Chassis1.sch, Chassis2.brd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]
2021-06-30 updated Arduino labs
2021-07-23 changes to svg templates
    [Chassis2Smol.brd, Chassis2Smol.sch]
2021-08-12 minor fixes to esp32
2021-08-18 Added Pdfs
    [Chassis1.brd]
2021-08-20 Added diode protection board
    [BOM_Arduino_Nano.xlsx, BOM_ESP32.xlsx, Chasiss1.1.brd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]
2021-09-01 Fixed Issue with 3.3v regulator overpowering
    [BOM_Arduino_Nano.xlsx, Chasiss1.1.brd, Chasiss1.1.sch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]
2021-09-04 PCB and base changes
    [BOM_Arduino_Nano.xlsx, BOM_ESP32.xlsx]
2021-09-07 update to BOM
2021-09-20 added resistor to BOM
    [BOM_Arduino_Nano.xlsx]
2021-09-27 Reverse diode not needed, routing was done incorrectly by accident. Also added route from voltage regulator to the Arduino Nano for power. Updated some notes in the README and cleaned out some unused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
    [Chasiss1.1.brd, Chasiss1.1.sch]
2021-09-28 fix to power Arduino board
    [Chasiss1.1.sch]
2021-11-19 Added PCB layout PDF
2021-12-14 Improved grammer under PCB paragraph.
2021-12-14 links are good, typos are filtered out
2021-12-14 working chassis
2021-12-15 typos filtered out, hyperlinks work, page optimization
2021-12-15 typos filtered out, hyperlinks work
2021-12-15 Cleaned up, and fixed code issues
    [lab3.ino]
2021-12-15 Cleaned up code and bugs
    [Lab4.ino]
2022-01-06 updated PCB sizes
2022-01-11 updated PCB photo for reference
2022-02-08 updated wrong pwm pin
    [lab3.ino]
2022-02-15 updated 11 and 12 pin error to 6 and 7
    [Lab4.ino]
2022-10-31 Add JLC PCB Files

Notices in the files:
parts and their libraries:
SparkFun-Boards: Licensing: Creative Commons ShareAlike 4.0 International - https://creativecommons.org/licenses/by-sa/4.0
